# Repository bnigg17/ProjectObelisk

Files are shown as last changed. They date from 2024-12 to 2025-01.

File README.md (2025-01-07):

# Project Overview
Project Obelisk aimed to recreate and enhance the traditional key tag unlocking systems widely used for business security. Our approach replaces the physical key tag with a "custom key" powered by image recognition via artificial intelligence. The "custom key" can be any object that can be uniquely recognized, such as the back of your phone, a rubber duck, or even an apple. The system allows users to dynamically train and store custom keys, which are then used to activate a connected device, such as a servo motor. In our prototype, this servo motor simulates a door lock mechanism, showcasing the concept's functionality.

Demo

# About this Project
This project was developed over the course of 10 weeks for the Advanced Digital Systems Lab (ECE395) at UIUC. It involved the creation of a hardware-based system, where my partner and I individually or collaboratively explored the complexities of embedded systems, hardware design, and artificial intelligence. Our journey was marked by numerous challenges that required extensive research, documentation reading, and hands-on troubleshooting, pushing our knowledge and skills in electrical and embedded systems design to new limits.

# Project Obelisk
Project Obelisk is the main undertaking, designed as an all-in-one solution that integrates image processing, AI for object recognition, and a control loop to manage the servo motor and LED indicators. This system seamlessly ties together hardware and software components, allowing for dynamic key recognition and an output signal to trigger external devices.

# Project Obelisk Arduino / Raspberry Pi
The Arduino/Raspberry Pi subproject was designed as a testing environment for simpler systems and to verify our concept before moving to low-level C implementation. This step involved experimenting with synchronization signals, image array padding, and baud rate requirements for camera debugging. Using the Arduino/Raspberry Pi setup allowed us to handle some of the image processing off the primary microcontroller, providing valuable insights into data flow, timing, and system behavior.

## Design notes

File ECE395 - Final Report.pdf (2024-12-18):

# ECE 395

## Fall 2024

# Project Obelisk Final Report

Braden Nigg(bnigg2) and Ben Malone(bmalo4)

# Project Overview

Project Obelisk aimed to recreate and enhance the key tag unlocking systems commonly used for business security. Our variation eliminates the physical key tag, replacing it with a “custom key” powered by image recognition using artificial intelligence. An example of a “custom key” is really any object you could think of; the back of your phone, an apple, a rubber duck, ect. The final system allows users to train custom keys dynamically and generates an output signal to activate devices, such as a servo motor, which we used to simulate a door lock mechanism.

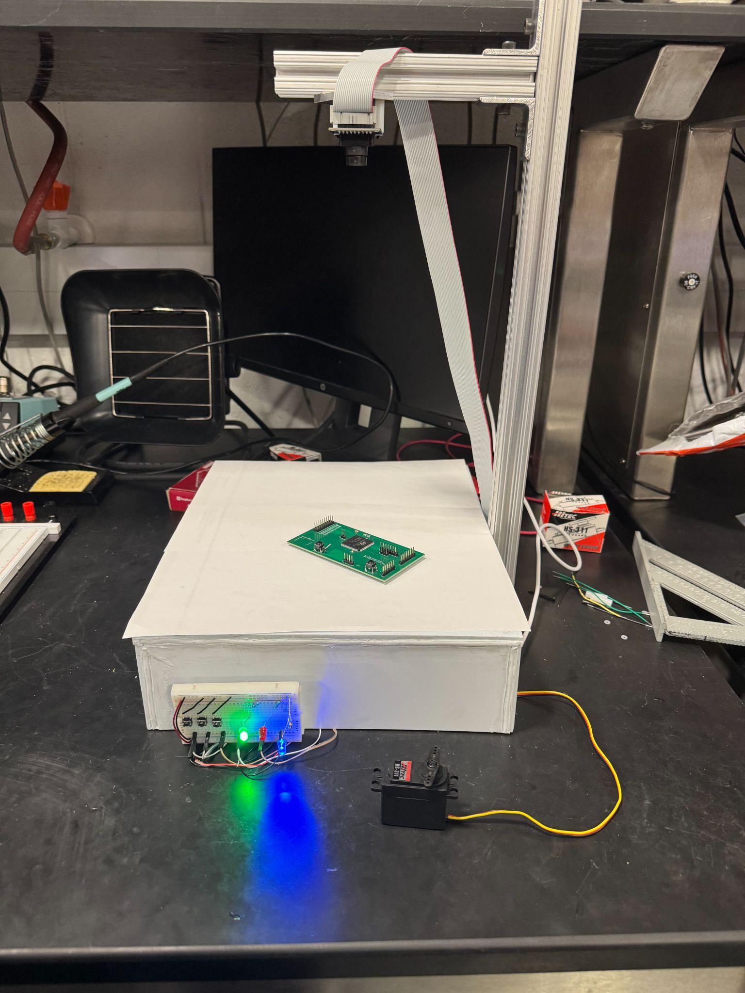
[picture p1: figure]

# Table of Contents

# System Architecture

## Components

The core component for object capture in Project Obelisk is the OV7670 camera. This camera supports a maximum resolution of 640x480 at 30 fps and offers various configurable settings for color, lighting, and scaling adjustments. It also includes an onboard algorithm for automatic image calibration, enhancing its adaptability to different environments.

Project Obelisk leverages the STM32 H7 series processor, selected for its high-frequency internal clock, which is crucial for driving the OV7670's master clock (MCLK). Additionally, its 2 MB of embedded SRAM provides sufficient capacity to run the lightweight AI algorithm utilized in the project.

The system's output component is the HS-422 servo motor. While the motor was chosen primarily for demonstration purposes in this project, those replicating the design should consider the required torque for their specific application. For our implementation, the HS-422 proved suitable for showcasing the unlocking mechanism.

## Debugging Components

We recommend using a UART device to transmit image captures to a more powerful system for analysis and validation during the calibration stages. Key considerations include the maximum baud rate supported by the UART device and the processing capability of the receiving system. For efficient transmission, we suggest a baud rate of at least 500,000 bits per second for lower resolution modes and exceeding 1 Mbit/s for full-resolution image captures. It is important to make sure the external system and the UART have matching baud rates to prevent corrupt data transmission.

## Block Diagram

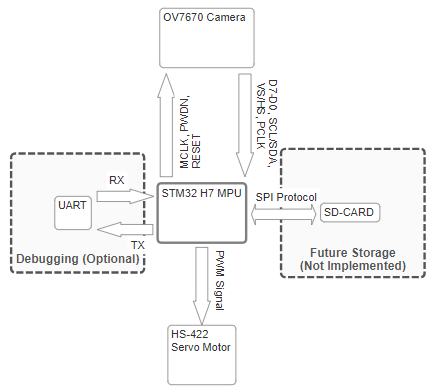
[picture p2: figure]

# Hardware Design

## Camera

The camera operates with Vcc and Vdd-IO expected at 3.0V, but it has an absolute maximum rating of 4.5V. We used 3.3V as the standard, which simplified the design by eliminating the need for additional voltage step-down circuitry.

The camera accepts a master clock input (MCLK) with a frequency range of 10–48 MHz; we chose the standard 24 MHz. However, testing revealed that the camera can operate at lower frequencies by leveraging its internal PLL (Phase Lock Loop), as described in the software section.

The pixel clock is an output signal that indicates when pixels are ready, with one pixel corresponding to two clock cycles. The camera also outputs Vsync (VS) and Hsync (HS) signals for synchronization. The Hsync signal can be modified to Href through register settings if required. In our design, these pins are not utilized as we implemented image capture based on a single snapshot. However, the Vsync signal can be valuable if the project is expanded to support a continuous live feed. Additionally, Hsync can be useful for debugging purposes, such as identifying line numbers or implementing line-based data transmissions.

Additionally, the camera provides Power Down (PWDN) and Reset pins, which can be used for power savings and setup control.

## SCCB Communication

The OV7670 camera uses the SCCB (Serial Camera Control Bus) protocol for hardware register communication. SCCB is very similar to the I2C protocol, with the key difference being that the SDA line can float in SCCB, whereas I2C requires a pull-up resistor. Despite this difference, the OV7670 can be successfully interfaced using I2C, as STM32 microcontrollers provide convenient drivers for I2C communication. By utilizing the transmit and receive functions provided by the STM32, it is possible to match the transmission sequence expected by the camera.

To ensure proper communication, pull-up resistors must be used for the SCL and SDA lines. A pull-up resistor value of 10kΩ is recommended, but it should not be lower than 4.7kΩ to maintain signal integrity. Additionally, the MCLK (Master Clock) signal must be connected to the camera; otherwise, I2C communication will not function correctly.

The OV7670 requires a 3-phase write cycle to modify its internal registers. First, a device address byte is sent, where the OV7670’s address is 0x42, with bit 0 set to 0 to indicate a write operation. If bit 0 is set to 1, it would instead indicate a read operation. Second, the subaddress byte specifies the register address to be written. Finally, a write data byte containing the desired data is transmitted to the selected register. By following this sequence, the OV7670 can reliably receive configuration data.

Reading data from the OV7670 camera follows a process similar to the write sequence but involves a 2-phase write followed by a 2-phase read. The first two bytes of the read process are identical to the 3-phase write sequence. First, the device address byte (0x42) with bit 0 set to 0 indicates a write operation, followed by the subaddress byte, which specifies the register address to be read.

After the subaddress is written, the process transitions to the read phase. Here, the device address is sent again, but this time bit 0 is set to 1, signaling a read operation. The camera then responds with the read data byte, which contains the value of the register specified in the earlier write phase. By following this sequence, the register value can be successfully read from the OV7670 camera.

SCCB Spec. Documentation

## Servo Motor

The servo motor features a simple hardware interface with a Vcc requirement of 5V, a ground connection, and a signal pin for motor control. The signal pin expects a 50 Hz PWM signal for operation. To generate this signal, we used a timer, as the required frequency is relatively slow compared to the system clock. The motor changes position based on pulse width of the PWM, and will be leveraged in the software section.

## Microcontroller

### DCMI/DMA

One of the key features of the high-performance STM32 processors is the DCMI (Digital Camera Memory Interface) driver, which simplifies the high-speed GPIO constraints when gathering image data. Enabling DCMI allows for fine control over synchronization, DMA configuration, clock signal polarity, and the specification of captured bytes and lines.

In our approach, we opted to read all bytes to capture complete pixel information and read all lines, as this allows for easier software manipulation of the image if needed. We also chose

DMA to reduce the number of read/write operations from the camera, as the pixel clock operates at speeds nearly matching that of the processor.

DMA also supports interrupts, which trigger a callback when the DMA transfer is complete, known as the frame event callback. For synchronization, we selected hardware synchronization, as the OV7670 camera generates its own hsync and vsync signals based on its internal clock and state. Finally, we specified the input as 8-bits, corresponding to D7-D0 on the OV7670, which is crucial for correctly aligning the DMA request in memory.

### Clocks

The MCU is configured to run at 168 MHz, which is more than sufficient for our use case. The primary requirement is that the AHB bus is at least 2.5 times faster than the pixel clock to ensure DMA can operate properly, as outlined in the STM32 DMA Configuration documentation. The main clock is derived from the internal high-speed clock (HSI), eliminating the need for an external oscillator. However, for greater precision, especially when working with PWM signals above 16 MHz, using an external oscillator may be preferable if available.

A Reset and Clock Control (RCC) option is used to generate a master clock out (MCO). This is necessary as timers are not clean enough at high frequencies. The MCO is configured at 24MHz and is a PLL divider down from the HSI clock.

### GPIOs and Serial Wire

Refer to the configuration document for full specifications. The I/O is primarily used to provide user control over the project’s state and to manage specific camera I/O functions. SWDIO and SWCLK are used for programming purposes and for debugging.

# Software Development

## Camera Register Setup

Below is a list of registers settings we used, there are many more and we highly recommend reading documentation. All registers are given by name and specific hex values can be found in documentation corresponding to name.

### QVGA Resolution

Register | Register Value | Description
COM3 | 0x04 | DCW - Enabled
COM14 | 0x19 | Manual scaling

SCALING_XSC | 0x3A | Scales X-Dir of Image Array
SCALING_YSC | 0x35 | Scales Y-Dir of Image Array
SCALING_DCWCTR | 0x11 | Downsampling and scaling control
SCALING_PCLK_DIV | 0xF1 | Pixel clock divider control
SCALING_PCLK_DELAY | 0x02 | Pixel clock delay control
Table 2-2 of OV7670 Implementation Guide

### RGB565 and Color Calibration

Register | Register Value | Description
COM7 | 0x04 | Camera control register, enables DCW (digital chroma width) processing.
RGB444 | 0x00 | Disable RGB444 settings
COM1 | 0x00 | Camera control register, disables CCIR656 format setting
COM15 | 0xD0 | Control for output format and compression, sets RGB output.
COM9 | 0x6A | Automatic gain control (AGC) settings, 128x Gain Ceiling
COM13 | 0x40 | Control for gamma correction, set saturation
MTX 1 | 0xB3 | Matrix coefficient 1, part of YUV to RGB conversion
MTX 2 | 0xB3 | Matrix coefficient 2, part of YUV to RGB conversion
MTX 3 | 0x00 | Matrix coefficient 3, part of YUV to RGB conversion
MTX 4 | 0x3D | Matrix coefficient 4, part of YUV to RGB conversion
MTX 5 | 0xA7 | Matrix coefficient 5, part of YUV to RGB conversion
MTX 6 | 0xE4 | Matrix coefficient 6, part of YUV to RGB conversion
Derived from Table 8-2 of OV7670 Implementation Guide Registers below the bolded line can be adjusted based on calibration needs. Registers above the bolded line are required for RGB565 to function properly.

### Frame Correction

Register | Register Value | Description
HSTART | 0x15 | Horizontal start position for the image frame. Affects where the capture begins.
HSTOP | 0x03 | Horizontal stop position for the image frame. Defines the end of the capture region in the horizontal direction.
HREF | 0x00 | Horizontal reference. Combines the start and stop positions to synchronize the horizontal scanning.
VSTART | 0x03 | Vertical start position for the image frame. Determines when the capture begins vertically.
VSTOP | 0x7B | Vertical stop position for the image frame. Defines the end of the capture region in the vertical direction.
VREF | 0x00 | Vertical reference. Combines the vertical start and stop positions to synchronize the vertical scanning.

Derived from Table 8-2 of OV7670 Implementation Guide This section may vary for each individual camera, so debugging and finding the correct values may be necessary. Essentially, it adjusts the window for capturing pixel data, where the start and stop values can behave in a modulo fashion.

### Frame Rate Control

Frame rate is crucial for continuous capture mode, but modifying the pixel clock is equally important, as synchronization signals depend on it. We chose to match the pixel clock to our master clock, which runs at 24 MHz. The camera features an internal PLL that can either be configured or bypassed. We decided to use the PLL because it produces a more stable, square pixel clock compared to the input master clock. The following equation shows how the pixel clock frequency is determined based on the input master clock.

To match obtain our 24MHz clock the following registers are manipulated:

Register | Register Value | Description
DLBV | 0x7A | Input clock x4, enable PLL
CLKRC | 0x01 | Cancels out the x4 multiplier
Derived from Table 3-2 of OV7670 Implementation Guide

## Control Flow

Our system runs continuously polling button GPIOs while in a ready state. Once a GPIO is pressed, a decoding function determines the expected next state, training one of the two images or activates the decider for if the inputted key is valid. Below is a flow graph of our system's high level control loop:

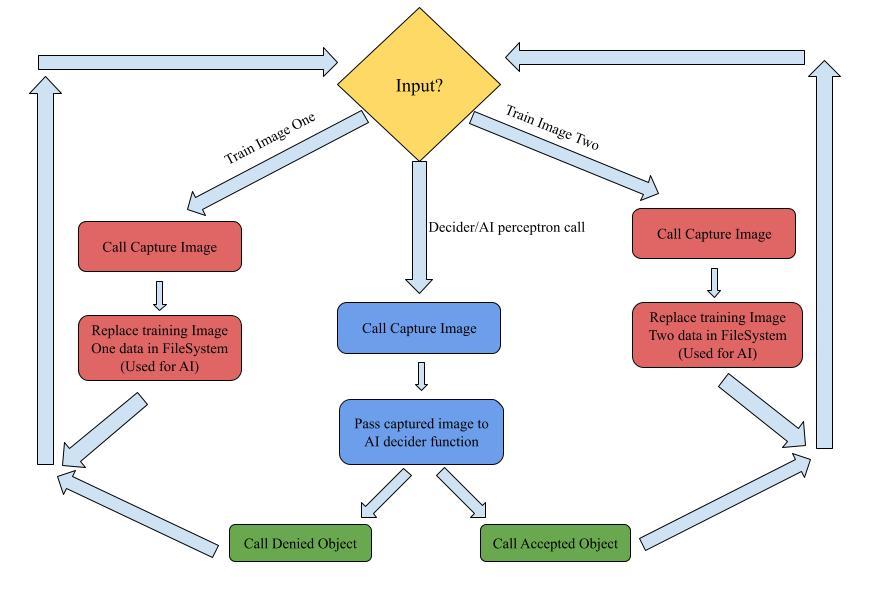
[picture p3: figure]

## Interrupts and Memory Management

Below is the memory layout for how our configured DCMI/DMA will place RGB565 values. Each word contains two pixels of complete information, as each pixel has 2 bytes of data.

Pixel X (D7 - D0) | Pixel X + 1 (D7 - D0)
RRRRRGGG | GGGBBBBB | RRRRRGGG | GGGBBBBB

With 2 MB of available embedded SRAM, we opted to create a global image buffer for the two trained images and the test image. Each image is approximately 230 KB in size when converted to RGB888, totaling 691 KB. We also have a buffer for the current capture, which is linked to our

DMA. This buffer is 153.6 KB in size, as each pixel requires two bytes from the camera. In total, 844 KB of space is required for storing the images.

The image capture works by signaling an interrupt when the DMA transfer is complete. We override the FrameEventCallback function to add our custom interrupt handler. This is where we signal that the image is ready for the intended purpose, as specified in the control loop.

## Artificial Intelligence

### Planning and System

The AI was trained on a much larger system. This allowed exploration of possibilities because of additional speed and memory, and for the ability to verify accuracy using lots of storage space for fake test images. Originally we attempted to explore the possibility of using a binary output neural network(perceptron), but because of memory constraints without off-chip memory, we had to come up with a different solution. Our solution was something like a baby-form of SURF or SIFT computer vision algorithms, which detect a variety of features about objects in images and make a decision upon them.

### Algorithm and Tuning

To be more specific, our algorithm runs an edge detection matrix multiplication on the image data in order to isolate the parts of the image which contain the object. From here a number of very defining features can be detected; object size in the specific frame, a number of different color average values, some features about the specific shape of the object. Lots of hard-tuning and auto-tuning went into finding optimized epsilon values for each of the different features, but in essence each object has a relatively personalized set of features within a reasonable epsilon which is additionally supported with a second reference image.

To ensure accuracy of the feature set method though, more data was needed to ensure that true key objects were accepted, and false images were denied(to a reasonable accuracy). So we created an image scraping tool using google images and selenium, gathered around a thousand images with a description matching the white-background environment, and tested and tuned our epsilon values again to increase accuracy. This tool and our accuracy analysis training code/tool are available in the linked github.

### AI limitations

While we put a lot of time into programming our AI code section, there are still strong limitations, as there are with all AI. Our less than 2MB ram shippable AI code is certainly no different and therefore some things won’t work. Most notably, the area in which images are taken from the camera must be where the entire object rests AND where the training images are taken. Otherwise the decider will hallucinate badly. Additionally, it is advised to avoid very non-unique objects, or objects lacking a specific color. For instance, if you trained the decider on your black wallet, there might be significant security issues considering how many black square shaped objects exist. Even worse, an all white object which could trick the edge detector, completely ruining all other feature detection mechanisms, obviously causing hallucinations.

## Servo Angle Control

As mentioned in the hardware section, the servo control input requires a 50 kHz PWM signal. To generate this signal, we need to configure the prescaler (PSC) and auto-reload register (ARR) of the timer.

For a 50 kHz PWM, we set PSC = 168-1 and ARR = 20-1. With these values, the timer produces the desired 50 kHz signal. Note these values can be of different multiples.

Next, to control the angle of the motor, we adjust the duty cycle. The following equation allows us to achieve the desired duty cycle based on the PWM period.

The key factor is that the servo motor's pulse width corresponds to the angle: a 2 ms pulse represents 180 degrees, and a 1 ms pulse represents 0 degrees. By manipulating the capture control register (CCR), we can generate the appropriate pulse width, thus controlling the motor's angle based on the desired state in the program.

# Challenges and Mitigation to Demo

## Issues

### Nucleo Prototype

The project encountered several issues during the camera calibration stages, many of which were beyond our control. Late in development we suspected that our STM32 Nucleo prototype board had a short circuit early in development. However, the board was able to program and respond to modifications for several weeks alluding us to think it was code related.

Later, we faced an issue while erasing part of the flash memory during programming. Online sources suggest this could be a command byte issue in the bootloader. However, we encountered the same problem during the PCB building stage, when the board was shorted indicating the protoboard was certainly damaged. When this error occurred on the prototype board, we could temporarily bypass it by over-volting the board, though this led to unstable behavior and program crashes.

### Custom PCB

In the PCB building phase, we successfully powered two PCBs, but after some testing, we suspected issues with both. The first PCB worked for a short time before encountering a debug authentication error during programming. This required us to drive the boot pin to boot from a different region. Further testing revealed(or maybe caused) that the board was shorted, causing the current to drop and leading to unstable program behavior. We are unsure if the debug authentication was an issue related to the hardware configuration or an advanced feature pertaining to the high end STM32 H7 chip.

The second PCB had a significant ground issue, which manifested as a triangular sine wave on the oscilloscope. Due to these challenges, we eventually ported our code and knowledge to an Arduino for demo purposes.

## Arduino Setup

### Arduino-Raspberry Pi Demo Block Diagram

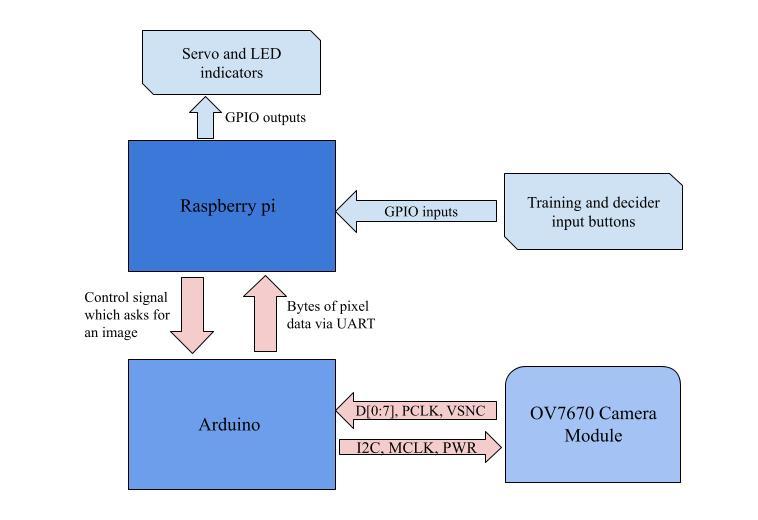
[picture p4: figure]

Our Arduino-based demo prototype required a different approach due to the limited onboard memory compared to the STM32 chip. Specifically, the Arduino lacked sufficient memory to store even a single image buffer, which made running the AI on-chip impossible. To work around this, we sent pixel data byte by byte through the UART serial line to a Raspberry Pi, which handled the memory constraints. Although we initially faced challenges with byte alignment, we were able to resolve them successfully.

Once the data reached the Raspberry Pi, it took over the processing, running a simple control loop and executing the AI code on the images received from the camera. For GPIO control, the Raspberry Pi provided a straightforward infrastructure. Instead of sending control packets back to the Arduino, we managed the limited GPIO outputs directly from the Raspberry Pi.

### Key Differences in Arduino Code

Given the limited time constraints (about 2 days) of porting our STM32 infrastructure to an arduino uno R3 we opted for merging a premade OV7670 library with our code. As much of the camera is configured through registers, there were few adjustments to be made to these settings. However, the arduino diverged from our system with not supporting DMA. The library way of gathering pixel data was to manually poll the pixel clock GPIO pin and send over UART within a time constraint. We largely left this alone as we needed a working product for the camera. The downside of this approach is very slow image capture with the combination of a slowed pixel clock and UART speeds.

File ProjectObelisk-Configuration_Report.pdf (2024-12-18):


17/12/2024

ProjectObelisk Project
Configuration Report

## 1. Description

### 1.1. Project

Project Name | ProjectObelisk
Board Name | custom
Generated with: | STM32CubeMX 6.13.0
Date | 12/17/2024

### 1.2. MCU

MCU Series | STM32H7
MCU Line | STM32H7A3/7B3
MCU name | STM32H7A3ZITxQ
MCU Package | LQFP144
MCU Pin number | 144

### 1.3. Core(s) information

Core(s) | Arm Cortex-M7

## 2. Pinout Configuration

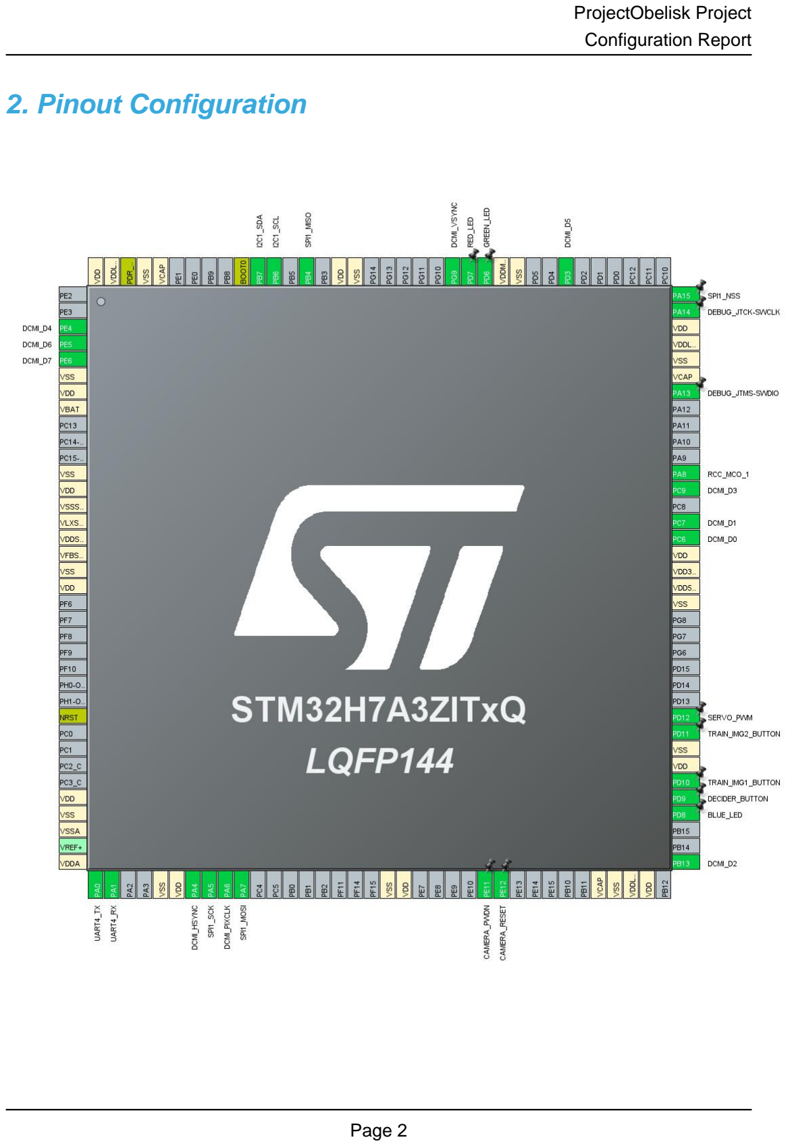
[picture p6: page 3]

## 3. Pins Configuration

Pin Number LQFP144 | Pin Name (function after reset) | Pin Type | Alternate Function(s) | Label
3 | PE4 | I/O | DCMI_D4
4 | PE5 | I/O | DCMI_D6
5 | PE6 | I/O | DCMI_D7
6 | VSS | Power
7 | VDD | Power
8 | VBAT | Power
12 | VSS | Power
13 | VDD | Power
14 | VSSSMPS | Power
15 | VLXSMPS | Power
16 | VDDSMPS | Power
17 | VFBSMPS | Power
18 | VSS | Power
19 | VDD | Power
27 | NRST | Reset
32 | VDD | Power
33 | VSS | Power
34 | VSSA | Power
36 | VDDA | Power
37 | PA0 | I/O | UART4_TX
38 | PA1 | I/O | UART4_RX
41 | VSS | Power
42 | VDD | Power
43 | PA4 | I/O | DCMI_HSYNC
44 | PA5 | I/O | SPI1_SCK
45 | PA6 | I/O | DCMI_PIXCLK
46 | PA7 | I/O | SPI1_MOSI
55 | VSS | Power
56 | VDD | Power
61 | PE11 * | I/O | GPIO_Output | CAMERA_PWDN
62 | PE12 * | I/O | GPIO_Output | CAMERA_RESET
68 | VCAP | Power
69 | VSS | Power
70 | VDDLDO | Power
71 | VDD | Power
73 | PB13 | I/O | DCMI_D2

Pin Number LQFP144 | Pin Name (function after reset) | Pin Type | Alternate Function(s) | Label
76 | PD8 * | I/O | GPIO_Output | BLUE_LED
77 | PD9 * | I/O | GPIO_Input | DECIDER_BUTTON
78 | PD10 * | I/O | GPIO_Input | TRAIN_IMG1_BUTTON
79 | VDD | Power
80 | VSS | Power
81 | PD11 * | I/O | GPIO_Input | TRAIN_IMG2_BUTTON
82 | PD12 | I/O | TIM4_CH1 | SERVO_PWM
89 | VSS | Power
90 | VDD50_USB | Power
91 | VDD33_USB | Power
92 | VDD | Power
93 | PC6 | I/O | DCMI_D0
94 | PC7 | I/O | DCMI_D1
96 | PC9 | I/O | DCMI_D3
97 | PA8 | I/O | RCC_MCO_1
102 | PA13 | I/O | DEBUG_JTMS-SWDIO
103 | VCAP | Power
104 | VSS | Power
105 | VDDLDO | Power
106 | VDD | Power
107 | PA14 | I/O | DEBUG_JTCK-SWCLK
108 | PA15 | I/O | SPI1_NSS
115 | PD3 | I/O | DCMI_D5
118 | VSS | Power
119 | VDDMMC | Power
120 | PD6 * | I/O | GPIO_Output | GREEN_LED
121 | PD7 * | I/O | GPIO_Output | RED_LED
122 | PG9 | I/O | DCMI_VSYNC
128 | VSS | Power
129 | VDD | Power
131 | PB4 | I/O | SPI1_MISO
133 | PB6 | I/O | I2C1_SCL
134 | PB7 | I/O | I2C1_SDA
135 | BOOT0 | Boot
140 | VCAP | Power
141 | VSS | Power
142 | PDR_ON | Reset
143 | VDDLDO | Power
144 | VDD | Power

* The pin is affected with an I/O function

## 4. Clock Tree Configuration

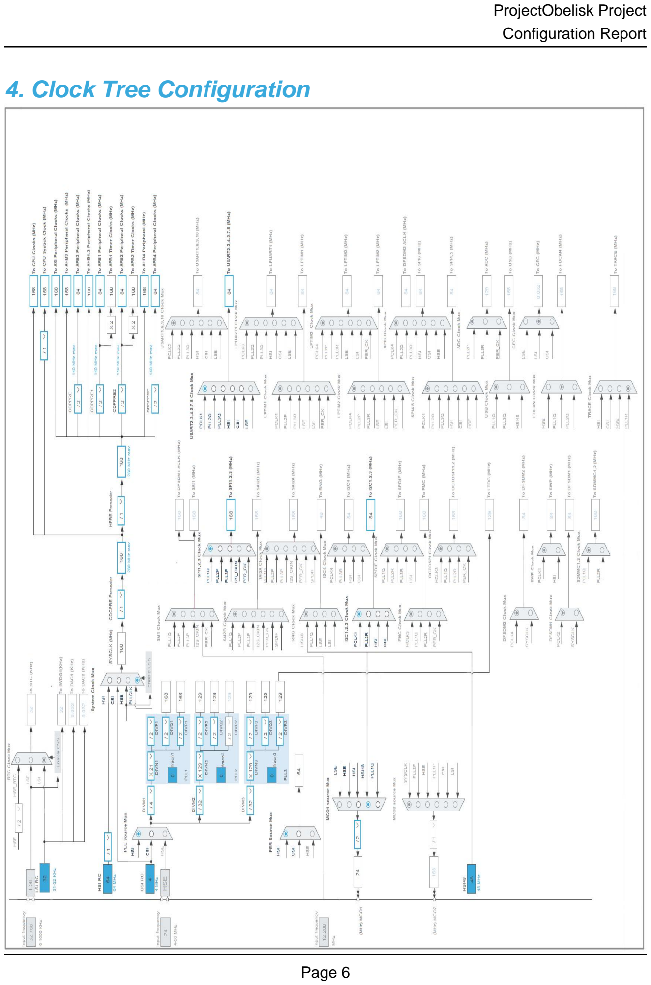
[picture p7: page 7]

## 1. Power Consumption Calculator report

### 1.1. Microcontroller Selection

Series | STM32H7
Line | STM32H7A3/7B3
MCU | STM32H7A3ZITxQ
Datasheet | DS13139_Rev0

### 1.2. Parameter Selection

Temperature | 25
Vdd | 3.0

### 1.3. Battery Selection

Battery | Li-SOCL2(A3400)
Capacity | 3400.0 mAh
Self Discharge | 0.08 %/month
Nominal Voltage | 3.6 V
Max Cont Current | 100.0 mA
Max Pulse Current | 200.0 mA
Cells in series | 1
Cells in parallel | 1

### 1.4. Sequence

Step | Step1 | Step2
Mode | RUN | STOP
Vdd | 3.0 | 3.0
Voltage Source | Battery | Battery
Range | VOS0 | SVOS5
SRDomain | DRUN | DSTOP
n/a | SRDRUN | SRDSTOP
Fetch Type | ITCM/DTCM/Cache | NA
CPU Frequency | 280 MHz | 64 MHz
Clock Configuration | HSE PLL | HSI Flash-ON
Clock Source Frequency | 16 MHz | 64 MHz
Peripherals
Additional Cons. | 0 mA | 0 mA
Average Current | 69.92 mA | 263.82 µA
Duration | 0.1 ms | 0.9 ms
DMIPS | 599.0 | 0.0
Ta Max | 115.77 | 124.97
Category | In DS Table | In DS Table

### 1.5. Results

Sequence Time | 1 ms | Average Current | 7.23 mA
Battery Life | 19 days, 14 hours Average DMIPS | | 599.2 DMIPS

### 1.6. Chart

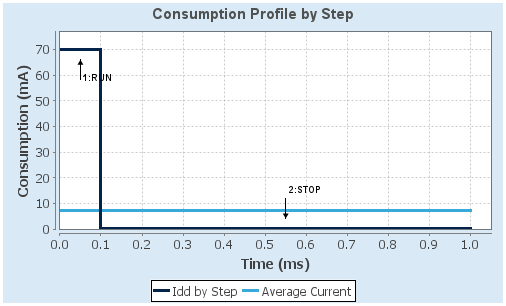
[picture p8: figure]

## 2. Software Project

### 2.1. Project Settings

Name | Value
Project Name | ProjectObelisk
Project Folder | C:\Users\BRADE\ECE395\ProjectObelisk
Toolchain / IDE | STM32CubeIDE
Firmware Package Name and Version | STM32Cube FW_H7 V1.12.0
Application Structure | Advanced
Generate Under Root | Yes
Do not generate the main() | No
Minimum Heap Size | 0x200
Minimum Stack Size | 0x400

### 2.2. Code Generation Settings

Name | Value
STM32Cube MCU packages and embedded software | Copy only the necessary library files
Generate peripheral initialization as a pair of '.c/.h' files | No
Backup previously generated files when re-generating | No
Keep User Code when re-generating | Yes
Delete previously generated files when not re-generated | Yes
Set all free pins as analog (to optimize the power consumption) | No
Enable Full Assert | No

### 2.3. Advanced Settings - Generated Function Calls

Rank | Function Name | Peripheral Instance Name
1 | SystemClock_Config | RCC
2 | MX_GPIO_Init | GPIO
3 | MX_DMA_Init | DMA
4 | MX_DCMI_Init | DCMI
5 | MX_I2C1_Init | I2C1
6 | MX_SPI1_Init | SPI1
7 | MX_UART4_Init | UART4
8 | MX_TIM4_Init | TIM4

## 3. Peripherals and Middlewares Configuration

### 3.1. CORTEX_M7

3.1.1. Parameter Settings:

Speculation default mode Settings:

Speculation default mode | Enabled *
Cortex Interface Settings:
CPU ICache | Disabled
CPU DCache | Disabled
Cortex Memory Protection Unit Control Settings:
MPU Control Mode | Background Region Privileged accesses only + MPU Disabled during hard fault, NMI and FAULTMASK handlers

Cortex Memory Protection Unit Region 0 Settings:

MPU Region | Enabled
MPU Region Base Address | 0x0 *
MPU Region Size | 4GB
MPU SubRegion Disable | 0x87 *
MPU TEX field level | level 0
MPU Access Permission | ALL ACCESS NOT PERMITTED
MPU Instruction Access | DISABLE
MPU Shareability Permission | ENABLE
MPU Cacheable Permission | DISABLE
MPU Bufferable Permission | DISABLE
Cortex Memory Protection Unit Region 1 Settings:
MPU Region | Disabled
Cortex Memory Protection Unit Region 2 Settings:
MPU Region | Disabled
Cortex Memory Protection Unit Region 3 Settings:
MPU Region | Disabled
Cortex Memory Protection Unit Region 4 Settings:
MPU Region | Disabled
Cortex Memory Protection Unit Region 5 Settings:
MPU Region | Disabled
Cortex Memory Protection Unit Region 6 Settings:
MPU Region | Disabled
Cortex Memory Protection Unit Region 7 Settings:
MPU Region | Disabled
Cortex Memory Protection Unit Region 8 Settings:
MPU Region | Disabled

Cortex Memory Protection Unit Region 9 Settings:

MPU Region | Disabled
Cortex Memory Protection Unit Region 10 Settings:
MPU Region | Disabled
Cortex Memory Protection Unit Region 11 Settings:
MPU Region | Disabled
Cortex Memory Protection Unit Region 12 Settings:
MPU Region | Disabled
Cortex Memory Protection Unit Region 13 Settings:
MPU Region | Disabled
Cortex Memory Protection Unit Region 14 Settings:
MPU Region | Disabled
Cortex Memory Protection Unit Region 15 Settings:
MPU Region | Disabled

### 3.2. DCMI

DCMI: Slave 8 bits External Synchro
3.2.1. Parameter Settings:

Mode Config:
Pixel clock polarity | Active on Rising edge *
Vertical synchronization polarity | Active High *
Horizontal synchronization polarity | Active Low
Frequency of frame capture | All frames are captured
JPEG mode | Disabled
Interface Capture Config:
Byte Select Mode | Interface captures all received bytes
Line Select Mode | Interface captures all received lines

### 3.3. DEBUG

Debug: Serial Wire

### 3.4. I2C1

I2C: I2C
3.4.1. Parameter Settings:

Timing configuration:

Custom Timing | Disabled
I2C Speed Mode | Standard Mode
I2C Speed Frequency (KHz) | 100
Rise Time (ns) | 0
Fall Time (ns) | 0
Coefficient of Digital Filter | 0
Analog Filter | Enabled
Timing | 0x10A0A4F8 *
Slave Features:
Clock No Stretch Mode | Disabled
General Call Address Detection | Disabled
Primary Address Length selection | 7-bit
Dual Address Acknowledged | Disabled
Primary slave address | 0

### 3.5. MEMORYMAP

mode: Activated

### 3.6. RCC

mode: Master Clock Output 1
3.6.1. Parameter Settings:

Power Parameters:

SupplySource | PWR_DIRECT_SMPS_SUPPLY
Power Regulator Voltage Scale | Power Regulator Voltage Scale 1
RCC Parameters:
TIM Prescaler Selection | Disabled
HSE Startup Timout Value (ms) | 100
LSE Startup Timout Value (ms) | 5000
CSI Calibration Value | 16
HSI Calibration Value | 64
System Parameters:
VDD voltage (V) | 3.3
Flash Latency(WS) | 4 WS (5 CPU cycle)
PLL range Parameters:
PLL1 input frequency range | Between 8 and 16 MHz
PLL1 clock Output range | Wide VCO range

### 3.7. SPI1

Mode: Full-Duplex Master
Hardware NSS Signal: Hardware NSS Input Signal
3.7.1. Parameter Settings:

Basic Parameters:

Frame Format | Motorola
Data Size | 4 Bits
First Bit | MSB First
Clock Parameters:
Prescaler (for Baud Rate) | 2
Baud Rate | 84.0 MBits/s *
Clock Polarity (CPOL) | Low
Clock Phase (CPHA) | 1 Edge
Advanced Parameters:
CRC Calculation | Disabled
NSSP Mode | Enabled
NSS Signal Type | Input Hardware
Fifo Threshold | Fifo Threshold 01 Data
Tx Crc Initialization Pattern | All Zero Pattern
Rx Crc Initialization Pattern | All Zero Pattern
Nss Polarity | Nss Polarity Low
Master Ss Idleness | 00 Cycle
Master Inter Data Idleness | 00 Cycle
Master Receiver Auto Susp | Disable
Master Keep Io State | Master Keep Io State Disable
IO Swap | Disabled

### 3.8. SYS

Timebase Source: SysTick

### 3.9. TIM4

Clock Source : Internal Clock Channel1: PWM Generation CH1
3.9.1. Parameter Settings:

Counter Settings:

Prescaler (PSC - 16 bits value) | 168-1 *
Counter Mode | Up
Counter Period (AutoReload Register - 16 bits value ) | 20-1 *
Internal Clock Division (CKD) | No Division
auto-reload preload | Disable
Trigger Output (TRGO) Parameters:
Master/Slave Mode (MSM bit) | Disable (Trigger input effect not delayed)
Trigger Event Selection TRGO | Reset (UG bit from TIMx_EGR)
Clear Input:
Clear Input Source | Disable
PWM Generation Channel 1:
Mode | PWM mode 1
Pulse (16 bits value) | 0
Output compare preload | Enable
Fast Mode | Disable
CH Polarity | High

### 3.10. UART4

Mode: Asynchronous
3.10.1. Parameter Settings:

Basic Parameters:

Baud Rate | 19200 *
Word Length | 8 Bits (including Parity)
Parity | None
Stop Bits | 1
Advanced Parameters:
Data Direction | Receive and Transmit
Over Sampling | 16 Samples
Single Sample | Disable
ClockPrescaler | 1
Fifo Mode | FIFO mode disable
Txfifo Threshold | 1 eighth full configuration
Rxfifo Threshold | 1 eighth full configuration
Advanced Features:
Auto Baudrate | Disable
TX Pin Active Level Inversion | Disable

RX Pin Active Level Inversion | Disable
Data Inversion | Disable
TX and RX Pins Swapping | Disable
Overrun | Enable
DMA on RX Error | Enable
MSB First | Disable

* User modified value

## 4. System Configuration

### 4.1. GPIO configuration

IP | Pin | Signal | GPIO mode | GPIO pull/up pull down | Max Speed | User Label
| | | | | *
| PE5 | DCMI_D6 | Alternate Function Push Pull | Pull-down * | Very High *
| PE6 | DCMI_D7 | Alternate Function Push Pull | Pull-down * | Very High *
| PA4 | DCMI_HSYNC | Alternate Function Push Pull | Pull-down * | Very High *
| PA6 | DCMI_PIXCLK | Alternate Function Push Pull | Pull-down * | Very High *
| PB13 | DCMI_D2 | Alternate Function Push Pull | Pull-down * | Very High *
| PC6 | DCMI_D0 | Alternate Function Push Pull | Pull-down * | Very High *
| PC7 | DCMI_D1 | Alternate Function Push Pull | Pull-down * | Very High *
| PC9 | DCMI_D3 | Alternate Function Push Pull | Pull-down * | Very High *
| PD3 | DCMI_D5 | Alternate Function Push Pull | Pull-down * | Very High *
| PG9 | DCMI_VSYNC | Alternate Function Push Pull | Pull-down * | Very High *
DEBUG | PA13 | DEBUG_JTMS-SWDIO | n/a | n/a | n/a
| PA14 | DEBUG_JTCK-SWCLK | n/a | n/a | n/a
I2C1 | PB6 | I2C1_SCL | Alternate Function Open Drain | No pull-up and no pull-down | Low
| PB7 | I2C1_SDA | Alternate Function Open Drain | No pull-up and no pull-down | Low
RCC | PA8 | RCC_MCO_1 | Alternate Function Push Pull | No pull-up and no pull-down | Very High *
SPI1 | PA5 | SPI1_SCK | Alternate Function Push Pull | No pull-up and no pull-down | Low
| PA7 | SPI1_MOSI | Alternate Function Push Pull | No pull-up and no pull-down | Low
| PA15 | SPI1_NSS | Alternate Function Push Pull | No pull-up and no pull-down | Low
DCMI | PE4 | DCMI_D4 | Alternate Function Push Pull | Pull-down * | Very High

IP | Pin | Signal | GPIO mode | GPIO pull/up pull down | Max Speed | User Label
| PB4 | SPI1_MISO | Alternate Function Push Pull | No pull-up and no pull-down | Low
TIM4 | PD12 | TIM4_CH1 | Alternate Function Push Pull | No pull-up and no pull-down | Low | SERVO_PWM
UART4 | PA0 | UART4_TX | Alternate Function Push Pull | No pull-up and no pull-down | Low
| PA1 | UART4_RX | Alternate Function Push Pull | No pull-up and no pull-down | Low
GPIO | PE11 | GPIO_Output | Output Push Pull | No pull-up and no pull-down | Low | CAMERA_PWDN
| PE12 | GPIO_Output | Output Push Pull | No pull-up and no pull-down | Low | CAMERA_RESET
| PD8 | GPIO_Output | Output Push Pull | No pull-up and no pull-down | Low | BLUE_LED
| PD9 | GPIO_Input | Input mode | No pull-up and no pull-down | n/a | DECIDER_BUTTON
| PD10 | GPIO_Input | Input mode | No pull-up and no pull-down | n/a | TRAIN_IMG1_BUTTON
| PD11 | GPIO_Input | Input mode | No pull-up and no pull-down | n/a | TRAIN_IMG2_BUTTON
| PD6 | GPIO_Output | Output Push Pull | No pull-up and no pull-down | Low | GREEN_LED
| PD7 | GPIO_Output | Output Push Pull | No pull-up and no pull-down | Low | RED_LED

### 4.2. DMA configuration

DMA request | Stream | Direction | Priority
DCMI | DMA1_Stream0 | Peripheral To Memory | Low

DCMI: DMA1_Stream0 DMA request Settings:

Mode: | Normal
Use fifo: | Disable
Peripheral Increment: | Disable
Memory Increment: | Enable *
Peripheral Data Width: | Word *
Memory Data Width: | Word

### 4.3. BDMA1 configuration

nothing configured in DMA service

### 4.4. BDMA2 configuration

nothing configured in DMA service

### 4.5. MDMA configuration

nothing configured in DMA service

### 4.6. NVIC configuration

4.6.1. NVIC
Interrupt Table | Enable | Preenmption Priority | SubPriority
Non maskable interrupt | true | 0 | 0
Hard fault interrupt | true | 0 | 0
Memory management fault | true | 0 | 0
Pre-fetch fault, memory access fault | true | 0 | 0
Undefined instruction or illegal state | true | 0 | 0
System service call via SWI instruction | true | 0 | 0
Debug monitor | true | 0 | 0
Pendable request for system service | true | 0 | 0
System tick timer | true | 15 | 0
DMA1 stream0 global interrupt | true | 0 | 0
DCMI and PSSI global interrupt | true | 0 | 0
PVD and PVM interrupts through EXTI line | unused
Flash global interrupt | unused
RCC global interrupt | unused
TIM4 global interrupt | unused
I2C1 event interrupt | unused
I2C1 error interrupt | unused
SPI1 global interrupt | unused
UART4 global interrupt | unused
FPU global interrupt | unused
HSEM1 global interrupt | unused
4.6.2. NVIC Code generation
Enabled interrupt Table | Select for init sequence ordering | Generate IRQ handler | Call HAL handler
Non maskable interrupt | false | true | false
Hard fault interrupt | false | true | false
Memory management fault | false | true | false
Pre-fetch fault, memory access fault | false | true | false
Undefined instruction or illegal state | false | true | false
System service call via SWI instruction | false | true | false
Debug monitor | false | true | false
Pendable request for system service | false | true | false
System tick timer | false | true | true
DMA1 stream0 global interrupt | false | true | true
DCMI and PSSI global interrupt | false | true | true

* User modified value

## 5. System Views

5.1. Category view
5.1.1. Current

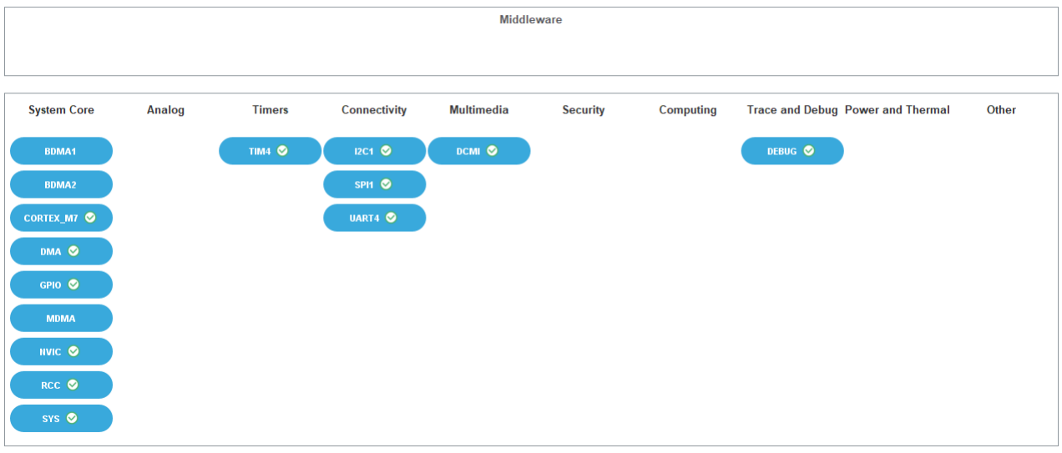
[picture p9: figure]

## 6. Docs & Resources

Type | Link
BSDL files | https://www.st.com/resource/en/bsdl_model/stm32h7_bsdl.zip
IBIS models | https://www.st.com/resource/en/ibis_model/stm32h7_ibis.zip
System View Description | https://www.st.com/resource/en/svd/stm32h7-svd.zip
Presentations | https://www.st.com/resource/en/product_presentation/microcontrollers_stm32h7_series_product_overview.pdf
Presentations | https://www.st.com/resource/en/product_presentation/stm32-stm8_embedded_software_solutions.pdf
Presentations | https://www.st.com/resource/en/product_presentation/stm32_eval-tools_portfolio.pdf
Presentations | https://www.st.com/resource/en/product_presentation/stm32_stm8_functi onal-safety-packages.pdf
Presentations | https://www.st.com/resource/en/product_presentation/stm32-stm8_software_development_tools.pdf
Presentations | https://www.st.com/resource/en/product_presentation/microcontrollers_stm32h7a3-b3_line_product-overview.pdf
Presentations | https://www.st.com/resource/en/product_presentation/microcontrollers-stm32-family-overview.pdf
Presentations | https://www.st.com/resource/en/product_presentation/microcontrollers-stm32h7rs-lines-overview.pdf
Brochures | https://www.st.com/resource/en/brochure/brstm32h7.pdf
Brochures | https://www.st.com/resource/en/brochure/products-and-solutions-for-plcs-and-smart-i-os.pdf
Flyers | https://www.st.com/resource/en/flyer/flstm32nucleo.pdf
Flyers | https://www.st.com/resource/en/flyer/flstm32trust.pdf
Flyers | https://www.st.com/resource/en/flyer/flstm32h7rs.pdf
Application Notes | https://www.st.com/resource/en/application_note/an1709-emc-design-guide-for-stm8-stm32-and-legacy-mcus-stmicroelectronics.pdf
Application Notes | https://www.st.com/resource/en/application_note/an2606-stm32-

| microcontroller-system-memory-boot-mode-stmicroelectronics.pdf
Application Notes | https://www.st.com/resource/en/application_note/an2639-soldering-recommendations-and-package-information-for-leadfree-ecopack-mcus-and-mpus-stmicroelectronics.pdf
Application Notes | https://www.st.com/resource/en/application_note/an3126-audio-and-waveform-generation-using-the-dac-in-stm32-products-stmicroelectronics.pdf
Application Notes | https://www.st.com/resource/en/application_note/an3155-usart-protocol-used-in-the-stm32-bootloader-stmicroelectronics.pdf
Application Notes | https://www.st.com/resource/en/application_note/an3156-usb-dfu-protocol-used-in-the-stm32-bootloader-stmicroelectronics.pdf
Application Notes | https://www.st.com/resource/en/application_note/an4221-i2c-protocol-used-in-the-stm32-bootloader-stmicroelectronics.pdf
Application Notes | https://www.st.com/resource/en/application_note/an4286-spi-protocol-used-in-the-stm32-bootloader-stmicroelectronics.pdf
Application Notes | https://www.st.com/resource/en/application_note/an4566-extending-the-dac-performance-of-stm32-microcontrollers-stmicroelectronics.pdf
Application Notes | https://www.st.com/resource/en/application_note/an4655-virtually-increasing-the-number-of-serial-communication-peripherals-in-stm32-applications-stmicroelectronics.p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
Application Notes | https://www.st.com/resource/en/application_note/an4750-handling-of-soft-errors-in-stm32-applications-stmicroelectronics.pdf
Application Notes | https://www.st.com/resource/en/application_note/an4776-generalpurpose-timer-cookbook-for-stm32-microcontrollers-stmicroelectronics.pdf
Application Notes | https://www.st.com/resource/en/application_note/an4803-highspeed-si-simulations-using-ibis-and-boardlevel-simulations-using-hyperlynx-si-on-stm32-mcus-and-mpus-stmic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
Application Notes | https://www.st.com/resource/en/application_note/an4839-level-1-cache-on-stm32f7-series-and-stm32h7-series-stmicroelectronics.pdf
Application Notes | https://www.st.com/resource/en/application_note/an4989-stm32-microcontroller-debug-toolbox-stmicroelectronics.pdf
Application Notes | https://www.st.com/resource/en/application_note/an4990-getting-started- with-sigmadelta-digital-interface-on-applicable-stm32-microcontrollers-

| stmicroelectronics.pdf
Application Notes | https://www.st.com/resource/en/application_note/an5020-digital-camera-interface-dcmi-on-stm32-mcus-stmicroelectronics.pdf
Application Notes | https://www.st.com/resource/en/application_note/an5027-interfacing-pdm-digital-microphones-using-stm32-mcus-and-mpus-stmicroelectronics.pdf
Application Notes | https://www.st.com/resource/en/application_note/an5033-stm32cube-mcu-package-examples-for-stm32h7-series-stmicroelectronics.pdf
Application Notes | https://www.st.com/resource/en/application_note/an5073-receiving-spdif-audio-stream-with-the-stm32f4f7h7-series-stmicroelectronics.pdf
Application Notes | https://www.st.com/resource/en/application_note/an5307-getting-started-with-stm32h7a37b3-line-and-stm32h7b0-value-line-microcontroller-hardware-development-stmicroel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
Application Notes | https://www.st.com/resource/en/application_note/an4899-stm32-microcontroller-gpio-hardware-settings-and-lowpower-consumption-stmicroelectronics.pdf
Application Notes | https://www.st.com/resource/en/application_note/an5450-stm32h7a37b3-lines-and-stm32h7b0-value-line-smart-power-management-expansion-package-for-stm32cube-stmicroelec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
Application Notes | https://www.st.com/resource/en/application_note/an5612-esd-protection-of-stm32-mcus-and-mpus-stmicroelectronics.pdf
Application Notes | https://www.st.com/resource/en/application_note/an5293-migration-guide-from-stm32f7-series-to-stmh74x75x-stm32h72x73x-and-stmh7a37bx-devices-stmicroelectronics.pdf
Application Notes | https://www.st.com/resource/en/application_note/an4838-introduction-to-memory-protection-unit-management-on-stm32-mcus-stmicroelectronics.pdf
Application Notes | https://www.st.com/resource/en/application_note/an5927-i3c-protocol-used-in-the-stm32-bootloader-stmicroelectronics.pdf
Application Notes | https://www.st.com/resource/en/application_note/an5225-introduction-to-usb-typec-power-delivery-for-stm32-mcus-and-mpus-stmicroelectronics.pdf
Application Notes | https://www.st.com/resource/en/application_note/an5342--how-to-use- error-correction-code-ecc-management-for-internal-memories-protection-

| on-stm32-mcus-stmicroelectronics.pdf
Application Notes | https://www.st.com/resource/en/application_note/an2834-how-to-optimize-the-adc-accuracy-in-the-stm32-mcus-stmicroelectronics.pdf
Application Notes | https://www.st.com/resource/en/application_note/an5537-how-to-use-adc-oversampling-techniques-to-improve-signaltonoise-ratio-on-stm32-mcus-stmicroelectronics.pdf
Application Notes | https://www.st.com/resource/en/application_note/an5036-guidelines-for-thermal-management-on-stm32-applications-stmicroelectronics.pdf
Application Notes | https://www.st.com/resource/en/application_note/an5405-how-to-use-fdcan-bootloader-protocol-on-stm32-mcus-stmicroelectronics.pdf
Application Notes | https://www.st.com/resource/en/application_note/an5690-how-to-use-vrefbuf-peripheral-on-stm32-mcus-and-mpus-stmicroelectronics.pdf
Application Notes | https://www.st.com/resource/en/application_note/an4230-introduction-to-random-number-generation-validation-using-the-nist-statistical-test-suite-for-stm32-mcus-and-m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
Application Notes | https://www.st.com/resource/en/application_note/an2867-guidelines-for-oscillator-design-on-stm8afals-and-stm32-mcusmpus-stmicroelectronics.pdf
Application Notes | https://www.st.com/resource/en/application_note/an4013-introduction-to-timers-for-stm32-mcus-stmicroelectronics.pdf
Application Notes | https://www.st.com/resource/en/application_note/an4277-how-to-use-pwm-shutdown-for-motor-control-and-digital-power-conversion-on-stm32-mcus-stmicroelectronics.pdf
Application Notes | https://www.st.com/resource/en/application_note/an4635-how-to-optimize-lpuart-power-consumption-on-stm32-mcus-stmicroelectronics.pdf
Application Notes | https://www.st.com/resource/en/application_note/an4759-introduction-to-using-the-hardware-realtime-clock-rtc-and-the-tamper-management-unit-tamp-with-stm32-mcus-stmi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
Application Notes | https://www.st.com/resource/en/application_note/an4861-introduction-to-lcdtft-display-controller-ltdc-on-stm32-mcus-stmicroelectronics.pdf
Application Notes | https://www.st.com/resource/en/application_note/an4908-getting-started- with-usart-automatic-baud-rater-detection-for-stm32-mcus-

| stmicroelectronics.pdf
Application Notes | https://www.st.com/resource/en/application_note/an4943-how-to-use-chromart-accelerator-to-refresh-an-lcdtft-display-on-stm32-mcus-stmicroelectronics.pdf
Application Notes | https://www.st.com/resource/en/application_note/an5156-introduction-to-security-for-stm32-mcus-stmicroelectronics.pdf
Application Notes | https://www.st.com/resource/en/application_note/an5200-getting-started-with-stm32h7-mcus-sdmmc-host-controller-stmicroelectronics.pdf
Application Notes | https://www.st.com/resource/en/application_note/an5224-introduction-to-dmamux-for-stm32-mcus-stmicroelectronics.pdf
Application Notes | https://www.st.com/resource/en/application_note/an5507-how-to-use-crc-to-check-the-integrity-of-the-internal-flash-memory-on-stm32h7-mcus-stmicroelectronics.pdf
Application Notes | https://www.st.com/resource/en/application_note/an5543-guidelines-for-enhanced-spi-communication-on-stm32-mcus-and-mpus-stmicroelectronics.pdf
Application Notes | https://www.st.com/resource/en/application_note/an5050-getting-started-with-octospi-hexadecaspi-and-xspi-interface-on-stm32-mcus-stmicroelectronics.pdf
Application Notes | https://www.st.com/resource/en/application_note/an4996-how-to-use-the-jpeg-codec-peripheral-on-stm32-mcus-stmicroelectronics.pdf
Application Notes | https://www.st.com/resource/en/application_note/an5348-introduction-to-fdcan-peripherals-for-stm32-mcus-stmicroelectronics.pdf
Application Notes for related Tools & Software | https://www.st.com/resource/en/application_note/an1202_freertos_guide-freertos-guide-stmicroelectronics.pdf
Application Notes for related Tools & Software | https://www.st.com/resource/en/application_note/an1602_semihosting_in_truestudio-how-to-do-semihosting-in-truestudio-stmicroelectronics.pdf
Application Notes for related Tools & Software | https://www.st.com/resource/en/application_note/an1801_stm32cubeprogrammer_in_truestudio-installing-stm32cubeprogrammer-in-truestudio-stmicroelectronics.pdf
Application Notes | https://www.st.com/resource/en/application_note/atollic_editing_keyboard

for related Tools & Software | _shortcuts-atollic-editing-keyboard-shortcuts-stmicroelectronics.pdf
Application Notes for related Tools & Software | https://www.st.com/resource/en/application_note/iar_to_atollic_truestudio_migration_guide-truestudio-for-arm-migration-guide-iar-embedded-workbench-to-truestudio-stm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
Application Notes for related Tools & Software | https://www.st.com/resource/en/application_note/stm32cubemx_installation_in_truestudio-stm32cubemx-installation-in-truestudio-stmicroelectronics.pdf
Application Notes for related Tools & Software | https://www.st.com/resource/en/application_note/an2606-stm32-microcontroller-system-memory-boot-mode-stmicroelectronics.pdf
Application Notes for related Tools & Software | https://www.st.com/resource/en/application_note/an4323-getting-started-with-stemwin-library-stmicroelectronics.pdf
Application Notes for related Tools & Software | https://www.st.com/resource/en/application_note/an4435-guidelines-for-obtaining-ulcsaiec-607301603351-class-b-certification-in-any-stm32-application-stmicroelectroni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
Application Notes for related Tools & Software | https://www.st.com/resource/en/application_note/an4657-stm32-inapplication-programming-iap-using-the-usart-stmicroelectronics.pdf
Application Notes for related Tools & Software | https://www.st.com/resource/en/application_note/an4841-digital-signal-processing-for-stm32-microcontrollers-using-cmsis-stmicroelectronics.pdf
Application Notes for related Tools & Software | https://www.st.com/resource/en/application_note/an4891-stm32h72x-stm32h73x-and-singlecore-stm32h74x75x-system-architecture-and-performance-stmicroelectronics.pdf
Application Notes for related Tools & Software | https://www.st.com/resource/en/application_note/an5001-stm32cube-expansion-package-for-stm32h7-series-mdma-stmicroelectronics.pdf
Application Notes for related Tools & Software | https://www.st.com/resource/en/application_note/an5014-stm32h7x3-smart-power-management-expansion-package-for-stm32cube-stmicroelectronics.pdf

Application Notes
for related Tools

https://www.st.com/resource/en/application_note/an5033-stm32cubemcu-package-examples-for-stm32h7-series-stmicroelectronics.pdf

& Software
Application Notes for related Tools & Software | https://www.st.com/resource/en/application_note/an5056-integration-guide-for-the-xcubesbsfu-stm32cube-expansion-package-stmicroelectronics.pdf
Application Notes for related Tools & Software | https://www.st.com/resource/en/application_note/an5360-getting-started-with-projects-based-on-the-stm32mp1-series-in-stm32cubeide-stmicroelectronics.pdf
Application Notes for related Tools & Software | https://www.st.com/resource/en/application_note/an5361-getting-started-with-projects-based-on-dualcore-stm32h7-microcontrollers-in-stm32cubeide-stmicroelectronics.pd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
Application Notes for related Tools & Software | https://www.st.com/resource/en/application_note/an5394-getting-started-with-projects-based-on-the-stm32l5-series-in-stm32cubeide-stmicroelectronics.pdf
Application Notes for related Tools & Software | https://www.st.com/resource/en/application_note/an5418-how-to-build-a-simple-usbpd-sink-application-with-stm32cubemx-stmicroelectronics.pdf
Application Notes for related Tools & Software | https://www.st.com/resource/en/application_note/an5426-migrating-graphics-middleware-projects-from-stm32cubemx-540-to-stm32cubemx-550-stmicroelectronics.pdf
Application Notes for related Tools & Software | https://www.st.com/resource/en/application_note/an5564-getting-started-with-projects-based-on-dualcore-stm32wl-microcontrollers-in-stm32cubeide-stmicroelectronics.pd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
Application Notes for related Tools & Software | https://www.st.com/resource/en/application_note/an4865-lowpower-timer-lptim-applicative-use-cases-on-stm32-mcus-and-mpus-stmicroelectronics.pdf
Application Notes for related Tools & Software | https://www.st.com/resource/en/application_note/an5698-adapting-the-xcubestl-functional-safety-package-for-stm32-iec-61508-compliant-to-other-safety-standards-stmicr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
Application Notes for related Tools & Software | https://www.st.com/resource/en/application_note/an5731-stm32cubemx-and-stm32cubeide-threadsafe-solution-stmicroelectronics.pdf
Application Notes for related Tools & Software | https://www.st.com/resource/en/application_note/an5450-stm32h7a37b3-lines-and-stm32h7b0-value-line-smart-power-management-expansion-package-for-stm32cube-stmicroelec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

Application Notes for related Tools & Software | https://www.st.com/resource/en/application_note/an4502-stm32-smbuspmbus-expansion-package-for-stm32cube-stmicroelectronics.pdf
Application Notes for related Tools & Software | https://www.st.com/resource/en/application_note/an5952-how-to-use-cmake-in-stm32cubeide-stmicroelectronics.pdf
Application Notes for related Tools & Software | https://www.st.com/resource/en/application_note/an4635-how-to-optimize-lpuart-power-consumption-on-stm32-mcus-stmicroelectronics.pdf
Application Notes for related Tools & Software | https://www.st.com/resource/en/application_note/an5054-how-to-perform-secure-programming-using-stm32cubeprogrammer-stmicroelectronics.pdf
Application Notes for related Tools & Software | https://www.st.com/resource/en/application_note/an6088-how-to-use-mce-for-encryptiondecryption-on-stm32-mcus-stmicroelectronics.pdf
Design Notes & Tips | https://www.st.com/resource/en/design_tip/dt0117-microphone-array-beamforming-in-the-pcm-and-pdm-domain-stmicroelectronics.pdf
Errata Sheets | https://www.st.com/resource/en/errata_sheet/es0478-stm32h7a3xig-stm32h7b0xb-and-stm32h7b3xi-device-errata-stmicroelectronics.pdf
Datasheet | https://www.st.com/resource/en/datasheet/dm00674683.pdf
Programming Manuals | https://www.st.com/resource/en/programming_manual/pm0253-stm32f7-series-and-stm32h7-series-cortexm7-processor-programming-manual-stmicroelectronics.pdf
Reference Manuals | https://www.st.com/resource/en/reference_manual/rm0455-stm32h7a37b3-and-stm32h7b0-value-line-advanced-armbased-32bit-mcus-stmicroelectronics.pdf
Technical Notes & Articles | https://www.st.com/resource/en/technical_note/tn1163-description-of-wlcsp-for-microcontrollers-and-recommendations-for-its-use-stmicroelectronics.pdf
Technical Notes & Articles | https://www.st.com/resource/en/technical_note/tn1204-tape-and-reel-shipping-media-for-stm32-microcontrollers-in-bga-packages-stmicroelectronics.pdf

Technical Notes
& Articles

https://www.st.com/resource/en/technical_note/tn1205-tape-and-reelshipping-media-for-stm8-and-stm32-microcontrollers-in-fpn-packages-

| stmicroelectronics.pdf
Technical Notes & Articles | https://www.st.com/resource/en/technical_note/tn1206-tape-and-reel-shipping-media-for-stm8-and-stm32-microcontrollers-in-qfp-packages-stmicroelectronics.pdf
Technical Notes & Articles | https://www.st.com/resource/en/technical_note/tn1207-tape-and-reel-shipping-media-for-stm8-and-stm32-microcontrollers-in-so-packages-stmicroelectronics.pdf
Technical Notes & Articles | https://www.st.com/resource/en/technical_note/tn1208-tape-and-reel-shipping-media-for-stm8-and-stm32-microcontrollers-in-tssop-and-ssop-packages-stmicroelectronics.p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
Technical Notes & Articles | https://www.st.com/resource/en/technical_note/tn1433-reference-device-marking-schematics-for-stm32-microcontrollers-and-microprocessors-stmicroelectronics.pdf
Technical Notes & Articles | https://www.st.com/resource/en/technical_note/tn1489-security-bulletin-tn1489stpsirt-physical-attacks-on-stm32-and-stm32cube-firmware-stmicroelectronics.pdf
User Manuals | https://www.st.com/resource/en/user_manual/um2840-stm32h7-dualcore-series-safety-manual-stmicroelectronics.pdf
User Manuals | https://www.st.com/resource/en/user_manual/um2331-stm32h7-singlecore-series-safety-manual-stmicroelectronics.pdf
User Manuals | https://www.st.com/resource/en/user_manual/um3252-stm32h7-series-ulcsaiec-607301603351-selftest-library-user-guide-stmicroelectronics.pdf

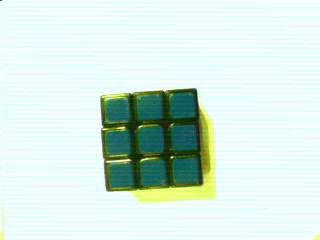
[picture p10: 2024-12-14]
ProjectObelisk_RaspPI_Arduino/Rasp_PI/training_2.png

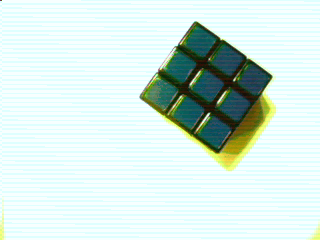
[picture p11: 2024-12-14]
ProjectObelisk_RaspPI_Arduino/Rasp_PI/training_1.png

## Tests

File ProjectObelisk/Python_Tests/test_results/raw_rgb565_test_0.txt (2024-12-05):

(90,91,253) (249,11,167) (11,237,107) (251,59,253) (249,39,11) (237,127,253) (153,11,237) (253,253,227) (195,227,195) (159,191,191) (191,95,95) (95,88,88) (88,112,88) (90,90,253) (251,253,253) (253,153,153) (57,253,141) (13,249,9) (9,237,253) (157,9,253) (153,137,139) (123,219,253) (123,251,253) (253,251,201) (43,253,253) (251,11,253) (227,251,11) (253,249,251) (237,253,253) (155,189,127) (249,139,127) (253,251,11) (253,253,47) (11,127,249) (45,237,127) (249,219,253) (253,249,131) (127,253,251) (45,253,253) (251,11,253) (253,243,253) (253,251,131) (253,253,39) (43,253,249) (219,123,237) (237,237,123) (253,253,25) (253,153,9) (227,11,249) (237,237,123) (123,253,155) (167,11,43) (253,123,249) (173,123,253) (249,249,155) (11,123,251) (251,253,217) (123,253,127) (253,249,153) (139,11,11) (127,253,249) (249,11,123) (253,235,155) (195,155,227) (211,195,195) (191,235,249) (253,249,153) (153,139,9) (231,239,75) (123,123,123) (123,43,123) (237,123,237) (123,253,251) (251,235,251) (203,251,235) (235,195,251) (251,251,251) (253,237,237) (237,251,251) (251,123,253) (251,251,235) (251,195,251) (251,251,251) (251,123,251) (251,251,251) (235,235,13) (253,253,191) (137,9,11) (11,107,43) (237,237,237) (251,9,11) (247,253,237) (237,237,237) (237,251,251) (251,123,11) (25,237,253) (253,251,251) (123,237,237) (237,237,123) (237,123,253) (253,249,153) (11,137,11) (9,9,11) (247,11,139) (237,237,253) (253,253,219) (191,223,123) (139,11,11) (237,253,127) (153,217,11) (11,237,253) (253,253,253) (185,153,139) (11,155,11) (237,123,237) (251,11,253) (253,251,253) (253,25,253) (249,153,157) (253,253,61) (253,9,251) (237,123,123) (251,251,253) (253,249,249) (183,139,11) (237,123,123) (253,253,249) (139,237,237) (123,123,253) (253,253,249) (253,155,155) (11,11,253) (127,253,253) (253,155,155) (11,43,127) (123,253,253) (249,153,139) (123,123,253) (255,253,253) (237,237,237) (251,123,123) (123,105,9) (11,9,141) (9,249,195) (195,235,195) (227,147,251) (203,251,123) (123,11,123) (11,9,9) (141,9,253) (13,253,253) (253,253,253) (235,251,251) (251,251,237) (237,237,237) (123,237,75) (123,107,11) (41,11,9) (191,191,155) (195,195,195) (195,195,251) (251,251,251) (251,251,251) (123,251,251) (9,107,75) (11,9,9) (9,157,13) (157,253,253) (253,237,251) (123,107,11) (9,147,203) (251,123,237) (251,9,251) (9,191,187) (195,251,251) (251,123,107)
(9,9,189) (253,237,237) (237,191,95) (247,115,191) (191,223,191) (241,191,191) (191,243,255) (191,191,241) (247,191,111) (225,229,223) (249,251,173) (237,237,123) (237,237,123) (123,251,139) (251,237,251) (253,251,253) (253,253,253) (253,253,253) (253,9,249) (155,11,11) (107,139,123) (123,123,237) (237,251,43) (11,9,9) (13,13,109) (251,123,251) (9,191,195) (195,235,251) (251,13,45) (237,237,123) (237,237,251) (123,11,29) (237,251,251) (251,123,123) (73,203,251) (251,251,107) (9,237,13) (253,237,237) (251,251,251) (107,237,9) (9,61,237) (253,237,251) (251,123,251) (123,107,9) (13,29,253) (253,237,251) (251,123,237) (75,105,9) (157,247,253) (235,251,251) (251,123,251) (107,9,9) (13,13,253) (237,253,237) (251,123,123) (231,9,9) (25,13,237) (251,251,251) (251,123,123) (107,9,9) (153,45,253) (253,251,251) (251,237,123) (107,105,9) (13,195,195) (251,251,251) (123,237,123) (251,237,45) (237,251,251) (123,9,9) (237,45,251) (237,251,123) (11,9,13) (253,237,237) (237,123,107) (9,247,9) (13,251,123) (237,9,11) (195,251,251) (251,251,13) (191,195,251) (251,123,123) (107,11,13) (45,237,237) (251,251,9) (9,25,253) (195,251,251) (251,251,123) (123,237,11) (247,13,251) (251,13,251) (121,77,251) (251,45,45) (251,109,13) (251,251,73) (13,109,237) (73,45,251) (13,251,127) (131,251,237) (13,251,237) (45,249,13) (251,77,251) (253,13,251) (205,251,251) (13,251,249) (77,45,131) (131,249,205) (251,253,139) (251,237,13) (251,255,131) (251,131,251) (205,251,253) (141,119,179) (253,219,253) (55,253,119) (253,251,237) (119,205,253) (251,237,251) (253,249,253) (253,179,253) (139,253,251) (237,103,131) (253,139,253) (187,13,125) (205,253,163) (253,139,179) (251,253,55) (131,253,251) (205,253,139) (253,139,205) (251,77,253) (13,51,253) (219,253,253) (179,249,139) (237,251,205) (253,251,131) (253,251,253) (253,253,253) (253,139,253) (251,205,253) (39,127,253) (131,253,249) (205,253,219) (221,249,139) (249,13,253) (205,249,51) (253,253,29) (253,55,253) (123,253,249) (155,123,253) (139,63,253) (139,187,249) (139,127,187) (139,253,253) (153,221,253) (253,253,221) (253,231,217) (221,127,253) (119,249,51) (253,253,253) (253,253,253) (155,51,253) (253,143,253) (249,141,253) (255,139,127) (253,3,59) (253,253,157) (253,253,187) (131,253,253) (251,253,127) (185,213,253) (253,249,221) (127,253,255) (51,253,253) (221,253,253) (251,35,253)
(253,139,127) (253,249,137) (253,253,253) (139,253,253) (253,219,51) (253,153,131) (253,253,249) (35,205,253) (249,163,253) (253,157,221) (253,253,139) (51,127,253) (185,221,253) (253,253,205) (253,253,249) (221,127,253) (155,221,253) (249,3,237) (253,253,131) (253,119,137) (253,253,157) (179,253,249) (35,131,255) (253,187,221) (221,253,253) (153,35,253) (255,249,35) (253,253,155) (131,253,55) (219,253,253) (185,35,221) (179,253,13) (253,251,253) (249,179,253) (141,253,249) (253,253,205) (253,139,237) (249,179,253) (139,253,251) (205,253,139) (253,251,205) (249,77,253) (139,253,47) (221,249,131) (253,219,253) (251,131,249) (13,253,251) (253,251,205) (119,139,127) (251,253,251) (179,253,45) (127,251,237) (249,13,253) (219,237,249) (131,253,251) (253,249,253) (253,249,13) (253,249,251) (253,251,115) (253,253,141) (253,251,139) (253,251,237) (249,131,253) (139,127,249) (77,127,251) (237,249,221) (249,131,253) (219,253,249) (139,253,251) (253,249,205) (221,251,131) (253,13,253) (187,29,253) (7,253,155) (51,253,29) (139,253,251) (253,251,253) (253,13,251) (13,251,77) (251,253,249) (249,45,249) (131,251,187) (251,77,45) (249,13,249) (13,251,205) (45,237,13) (251,13,109) (237,45,249) (131,251,77) (251,191,139) (253,77,249) (237,251,205) (249,13,253) (63,253,251) (77,251,139) (249,237,251) (13,111,187) (251,77,109) (205,251,249) (13,249,13) (253,139,237) (253,13,253) (251,253,253) (141,253,251) (127,251,77) (249,131,249) (13,253,139) (253,251,253) (109,253,45) (191,251,253) (13,253,219) (237,251,205) (249,205,249) (203,249,203) (253,139,77) (249,251,253) (45,253,253) (13,127,251) (255,253,205) (253,251,253) (251,205,251) (77,251,59) (253,131,253) (251,253,45) (253,131,251) (221,253,13) (253,249,131) (253,251,237) (139,97,163) (251,205,251) (13,103,77) (251,205,251) (253,187,251) (77,109,253) (251,253,45) (253,139,127) (51,13,13) (249,131,251) (13,251,253) (13,249,13) (251,77,251) (131,249,179) (253,131,249) (13,249,13) (249,77,253) (13,249,131) (249,77,251) (253,13,247) (13,249,13) (249,191,251) (253,127,249) (179,249,187) (251,77,251) (253,131,251) (13,251,77) (219,179,251) (237,251,127) (251,253,13) (247,251,253) (251,253,251) (205,251,237) (139,187,251) (77,249,13) (253,251,205) (253,251,205) (253,13,251) (249,205,253) (139,147,251) (253,109,127) (249,205,251) (187,249,163) (249,13,251) (205,249,205) (251,237,251) (191,203,253) (203,253,139)
(253,13,253) (251,251,77) (251,187,251) (179,249,237) (251,127,251) (253,13,127) (251,253,131) (249,131,251) (205,251,191) (251,253,251) (205,253,251) (237,249,163) (249,13,253) (39,253,203) (253,13,237) (251,127,249) (13,251,13) (251,237,251) (127,251,253) (251,249,187) (251,205,251) (63,249,131) (253,13,253) (13,253,131) (253,203,249) (13,253,45) (253,251,191) (251,205,253) (141,253,45) (253,139,253) (13,253,131) (253,139,253) (251,237,253) (237,249,51) (127,253,179) (253,139,205) (249,205,249) (219,237,45) (191,251,127) (253,139,253) (251,253,247) (131,253,77) (251,13,249) (77,249,13) (253,13,253) (139,253,249) (205,249,163) (249,77,253) (179,99,163) (119,131,253) (29,253,249) (179,253,13) (253,251,249) (13,251,13) (251,13,253) (251,253,253) (13,253,253) (253,249,205) (249,205,249) (203,249,77) (251,77,219) (205,251,127) (253,13,253) (139,253,179) (253,131,249) (13,249,139) (127,251,253) (13,249,205) (253,127,249) (13,253,251) (251,13,45) (249,13,251) (251,77,251) (251,13,45) (251,77,203) (251,77,203) (251,77,251) (251,187,251) (121,123,73) (13,237,237) (121,73,195) (219,251,251) (105,13,109) (237,251,105) (9,13,235) (251,251,73) (13,195,251) (251,73,191) (203,251,237) (251,253,251) (253,13,251) (187,251,237) (109,109,13) (251,13,251) (237,251,237) (251,127,139) (249,179,251) (253,249,253) (251,127,139) (253,45,253) (131,253,13) (253,205,253) (205,119,131) (251,77,251) (191,251,253) (251,253,13) (253,139,127) (139,253,131) (253,131,251) (187,251,237) (139,237,249) (13,253,139) (127,251,203) (249,139,127) (251,187,153) (249,253,249) (205,253,21) (253,251,131) (253,55,131) (253,141,221) (253,13,253) (249,131,253) (253,139,163) (253,253,139) (221,253,187) (205,253,253) (11,221,253) (253,219,253) (253,251,221) (29,253,249) (163,253,251) (141,249,139) (253,13,237) (191,139,237) (249,163,253) (219,253,251) (63,249,131) (253,203,253) (255,139,253) (253,139,253) (139,253,251) (127,249,221) (123,253,153) (221,253,253) (11,221,253) (253,23,253) (253,139,179) (253,251,205) (253,249,139) (253,253,185) (163,253,55) (221,253,153) (163,253,249) (131,253,253) (139,237,253) (155,93,251) (13,119,131) (253,251,237) (251,131,249) (77,253,249) (179,249,251) (237,249,205) (221,251,191) (251,141,253) (13,253,13) (253,13,205) (251,237,249) (237,249,77) (109,191,187) (195,203,249) (13,239,191) (203,249,13) (237,237,203) (119,179,251) (237,13,251) (13,251,249)
(131,251,77) (13,251,237) (45,249,13) (251,237,13) (251,13,251) (13,251,77) (253,139,253) (139,237,47) (253,251,253) (251,77,251) (13,253,139) (253,13,253) (251,205,249) (251,205,251) (163,249,251) (253,249,13) (249,13,253) (139,237,45) (179,249,139) (253,139,253) (187,221,251) (237,61,127) (251,77,249) (13,249,13) (253,141,93) (251,179,253) (13,253,251) (205,45,253) (131,249,205) (253,155,205) (253,13,127) (249,77,249) (205,253,13) (179,253,251) (205,253,251) (253,251,203) (253,219,127) (255,13,253) (249,205,251) (13,253,13) (253,251,253) (13,237,251) (77,251,179) (127,155,253) (249,13,253) (249,253,45) (191,251,237) (251,253,13) (251,253,139) (251,147,251) (13,251,249) (13,251,13) (45,249,13) (251,237,203) (237,13,249) (187,251,253) (251,253,139) (99,131,251) (77,251,253) (13,251,77) (251,253,219) (77,251,187) (249,13,237) (249,13,109) (77,251,249) (235,253,131) (253,13,47) (253,251,237) (45,247,139) (251,237,47) (13,45,249) (131,251,237) (45,237,249) (205,251,205) (251,203,249) (13,249,13) (249,139,253) (131,253,13) (119,179,253) (131,253,45) (253,203,253) (251,249,77) (249,13,249) (131,253,131) (253,131,253) (131,249,13) (253,139,249) (139,253,13) (253,249,221) (253,251,51) (253,55,205) (253,249,139) (253,251,205) (253,139,123) (253,93,253) (251,205,253) (155,237,255) (131,253,155) (221,251,205) (253,155,237) (249,13,253) (13,253,13) (253,251,253) (251,253,251) (187,251,253) (251,205,109) (253,251,163) (253,139,221) (119,131,253) (13,127,219) (253,251,77) (247,77,249) (77,251,77) (45,63,249) (13,251,205) (251,187,251) (253,251,249) (77,249,13) (251,77,251) (179,251,127) (251,253,219) (249,205,125) (253,251,127) (253,139,253) (45,127,249) (251,253,13) (127,251,205) (249,139,253) (13,253,251) (253,249,205) (253,203,253) (139,127,251) (253,251,179) (251,205,253) (13,253,249) (131,253,251) (51,253,205) (237,251,163) (253,13,127) (251,205,253) (139,253,249) (205,193,203) (127,139,253) (13,253,45) (253,251,255) (251,205,249) (205,249,13) (249,13,253) (13,253,13) (253,13,253) (39,237,251) (77,251,205) (247,13,249) (13,253,13) (253,139,253) (251,253,251) (77,45,13) (249,13,253) (251,253,13) (253,45,237) (249,139,253) (253,253,137) (131,253,253) (155,131,253) (253,139,123) (253,219,253) (55,163,253) (205,221,249) (139,253,251) (127,253,205) (253,13,247) (251,205,249) (139,253,251) (237,155,179) (249,139,253) (139,127,251)
(179,253,139) (253,251,187) (251,131,253) (251,127,249) (205,255,139) (253,253,237) (253,139,253) (253,155,131) (253,139,253) (63,23,253) (253,139,127) (249,205,131) (249,139,237) (45,253,251) (253,253,77) (253,139,253) (219,253,45) (253,13,253) (251,237,119) (205,249,131) (249,179,249) (131,251,205) (251,13,249) (13,253,251) (237,251,179) (187,29,249) (13,253,219) (253,251,253) (251,237,251) (255,251,205) (249,139,237) (55,139,253) (249,205,249) (141,253,251) (253,253,205) (251,205,119) (203,253,253) (237,251,127) (251,237,251) (205,251,191) (251,253,39) (205,249,219) (237,119,141) (253,45,249) (13,249,13) (119,139,237) (249,179,253) (251,255,253) (139,237,249) (35,253,251) (237,61,191) (251,237,155) (253,253,249) (131,253,55) (157,253,253) (31,253,253) (225,139,253) (253,253,131) (255,249,205) (253,253,31) (237,253,253) (221,255,253) (221,253,249) (237,253,249) (141,253,119) (139,253,253) (253,205,253) (253,141,253) (249,139,249) (13,249,139) (253,249,131) (59,253,155) (131,127,251) (253,251,187) (253,139,253) (139,187,253) (139,187,253) (115,253,139) (253,253,13) (253,253,253) (115,253,253) (251,205,253) (139,237,249) (141,127,249) (205,253,249) (127,253,13) (253,249,205) (253,29,123) (253,251,205) (249,179,253) (163,255,249) (205,253,249) (131,127,253) (131,127,249) (205,253,249) (139,237,253) (251,59,253) (153,139,253) (21,221,253) (139,221,127) (253,163,253) (249,205,115) (253,253,249) (139,253,253) (253,139,253) (253,253,131) (253,247,139) (205,253,249) (205,253,253) (155,51,253) (253,219,253) (253,251,51) (253,251,51) (253,249,131) (253,23,139) (127,253,139) (253,253,139) (127,253,139) (253,253,29) (253,249,29) (253,253,221) (253,253,139) (123,253,249) (143,127,249) (139,253,253) (131,253,249) (131,253,249) (205,253,251) (221,253,141) (223,253,249) (131,253,119) (139,131,253) (139,253,253) (137,63,253) (249,179,253) (21,139,253) (253,155,221) (127,249,205) (253,251,139) (253,139,253) (249,51,253) (251,77,253) (251,77,253) (249,237,119) (139,253,251) (77,251,187) (251,77,251) (205,251,237) (251,77,251) (205,249,77) (251,127,251) (205,249,179) (249,203,253) (251,253,139) (253,203,253) (139,253,139) (253,251,237) (251,237,251) (237,253,141) (127,251,131) (249,251,253) (61,237,249) (139,253,131) (253,109,109) (131,251,77) (251,205,55) (131,253,45) (127,251,253) (253,139,253) (249,179,249) (13,253,13) (253,13,253) (251,179,249) (13,253,13) (253,45,237) (251,127,251)
(237,251,253) (139,249,13) (249,77,251) (205,251,187) (249,77,247) (205,249,205) (249,77,13) (251,195,235) (251,77,203) (251,237,251) (251,109,45) (237,251,251) (251,105,13) (237,247,13) (251,251,237) (45,237,255) (195,251,77) (45,249,219) (249,131,251) (253,203,253) (187,251,205) (245,237,251) (253,131,249) (13,251,109) (187,251,249) (77,109,237) (251,251,125) (13,253,13) (251,187,251) (237,45,249) (167,251,131) (251,237,109) (253,139,237) (203,251,77) (251,249,253) (251,13,237) (249,13,251) (77,109,253) (131,249,205) (251,237,251) (191,251,179) (249,131,251) (205,249,77) (249,205,253) (13,221,251) (205,249,13) (249,205,253) (139,253,13) (253,251,253) (251,253,251) (237,251,253) (251,205,119) (77,251,13) (251,127,251) (179,251,205) (253,251,237) (251,237,249) (13,249,139) (253,45,237) (251,205,249) (13,249,13) (119,23,205) (253,139,253) (249,163,253) (13,253,249) (253,253,163) (127,139,253) (249,253,249) (237,249,237) (119,131,249) (13,249,139) (127,131,249) (179,249,205) (109,237,251) (253,251,77) (249,163,253) (77,249,13) (251,77,249) (205,251,13) (251,77,251) (127,251,253) (249,59,253) (13,253,249) (205,253,219) (253,251,221) (249,13,237) (251,221,253) (139,253,253) (205,253,251) (179,253,205) (221,253,133) (253,253,139) (131,253,255) (253,253,139) (253,155,139) (253,251,51) (253,139,237) (249,163,253) (139,253,251) (77,249,219) (127,249,205) (253,29,205) (249,139,253) (251,205,249) (131,253,139) (253,55,205) (127,139,191) (251,141,253) (139,127,249) (51,253,13) (253,251,131) (253,13,253) (249,179,253) (139,253,251) (205,253,15) (253,253,163) (253,251,253) (249,205,253) (251,127,249) (13,253,251) (127,249,13) (253,251,253) (249,205,237) (251,187,249) (251,253,251) (237,253,179) (127,251,205) (249,139,253) (55,205,253) (139,253,249) (205,253,13) (253,251,205) (253,139,253) (249,205,253) (13,127,251) (187,249,139) (253,13,205) (249,13,253) (61,127,253) (141,253,251) (51,253,139) (237,251,205) (253,13,253) (251,205,227) (139,253,251) (237,249,77) (253,251,205) (249,139,127) (251,253,253) (29,237,253) (251,253,253) (139,123,253) (157,139,253) (23,123,253) (251,131,253) (253,141,253) (249,93,253) (253,13,253) (253,115,253) (253,137,221) (127,253,253) (221,115,253) (23,215,131) (253,253,221) (253,249,35) (253,253,157) (127,253,139) (253,253,221) (253,119,139) (253,255,155) (221,253,249) (131,253,249) (131,253,55) (131,127,249) (139,253,249) (139,127,253)
(139,253,253) (139,237,253) (253,155,253) (253,139,221) (253,251,115) (253,29,179) (249,13,253) (251,205,125) (221,253,137) (139,253,253) (139,255,255) (51,253,251) (253,253,13) (253,251,205) (253,139,253) (251,203,249) (77,249,203) (253,155,29) (253,249,139) (253,251,237) (251,13,249) (131,249,131) (253,13,253) (55,253,251) (205,249,179) (249,77,249) (131,249,139) (253,15,237) (251,127,249) (205,253,131) (249,13,253) (13,253,139) (237,139,205) (39,237,249) (205,253,13) (253,45,253) (251,205,55) (205,249,205) (249,77,253) (139,253,45) (127,251,253) (251,179,249) (77,249,13) (127,139,253) (45,253,251) (237,249,205) (119,13,231) (203,253,139) (253,139,127) (251,205,251) (179,253,29) (127,249,115) (253,251,205) (249,219,253) (219,127,249) (77,253,13) (253,251,163) (249,13,127) (249,205,249) (139,253,139) (123,253,13) (253,55,237) (251,131,231) (203,253,13) (253,139,237) (29,253,249) (139,253,249) (131,237,13) (253,131,253) (219,253,249) (205,253,13) (253,29,237) (253,127,251) (187,251,237) (119,77,249) (147,251,205) (249,13,251) (131,251,77) (251,237,253) (131,127,251) (253,251,253) (139,127,251) (253,249,253) (249,251,253) (253,131,253) (21,163,253) (251,187,249) (139,255,253) (255,249,215) (163,253,253) (249,221,51) (253,153,139) (127,127,153) (139,253,127) (217,131,63) (249,139,127) (231,139,59) (127,253,163) (127,253,139) (253,205,253) (155,205,251) (179,253,15) (253,219,253) (187,29,253) (251,205,253) (13,253,13) (253,13,253) (203,253,139) (253,249,139) (253,255,131) (249,237,253) (203,127,251) (253,139,253) (13,127,251) (253,139,13) (253,235,253) (251,253,47) (205,249,237) (251,237,45) (253,249,13) (253,139,253) (139,253,251) (253,13,253) (251,253,251) (237,251,77) (251,205,251) (13,251,163) (253,131,253) (13,127,163) (249,77,249) (205,253,251) (179,253,139) (253,251,77) (203,253,251) (253,13,127) (249,139,253) (39,127,251) (249,139,255) (249,205,253) (251,205,253) (251,51,253) (251,237,253) (55,139,253) (251,221,127) (251,35,127) (253,187,205) (253,249,3) (131,253,155) (205,127,139) (127,253,139) (253,249,143) (253,253,139) (253,253,139) (253,119,139) (253,29,63) (253,13,221) (253,251,205) (127,251,255) (191,139,221) (253,251,253) (253,251,253) (251,253,251) (205,253,139) (51,127,253) (221,163,253) (23,127,253) (23,221,253) (253,253,253) (151,255,221) (253,253,253) (253,253,139) (253,253,253) (153,139,253) (253,253,253) (215,115,253) (253,253,139)
(123,253,253) (189,9,221) (253,253,137) (221,127,253) (251,141,253) (253,135,253) (249,249,51) (253,249,139) (253,253,253) (221,253,55) (163,127,253) (251,253,127) (155,237,253) (237,251,205) (249,205,253) (13,253,251) (237,119,115) (191,131,127) (251,237,251) (77,249,205) (119,13,249) (205,127,251) (187,253,205) (249,139,253) (163,253,15) (253,251,237) (253,13,253) (219,253,61) (251,253,249) (251,253,55) (237,253,139) (253,251,205) (249,205,253) (139,253,251) (77,249,13) (253,251,127) (253,131,249) (13,253,249) (253,249,205) (249,131,253) (13,253,55) (205,249,205) (253,13,127) (251,253,39) (127,249,205) (249,205,249) (139,253,219) (205,249,131) (249,139,253) (15,77,253) (77,253,203) (253,251,237) (249,139,253) (251,131,251) (139,253,251) (237,251,59) (253,13,253) (251,127,249) (179,253,205) (227,219,253) (251,205,249) (77,253,13) (253,187,15) (249,139,253) (251,127,249) (205,103,139) (253,13,253) (249,131,253) (253,51,253) (249,205,253) (61,187,249) (205,249,251) (253,251,205) (253,139,249) (253,205,253) (45,123,251) (77,253,219) (205,253,45) (253,249,51) (253,249,13) (127,131,253) (219,205,251) (131,127,219) (179,249,139) (253,45,253) (249,77,253) (29,253,249) (31,253,39) (205,249,205) (253,203,253) (45,253,249) (51,127,251) (205,253,155) (187,249,255) (253,251,205) (249,139,253) (251,131,253) (139,253,251) (139,123,253) (253,23,127) (253,205,253) (253,187,221) (187,193,201) (35,127,127) (155,221,253) (251,179,249) (13,253,219) (205,249,139) (253,155,237) (253,139,253) (251,205,253) (13,253,251) (221,249,13) (253,251,205) (249,13,127) (251,205,253) (131,253,249) (179,253,139) (237,249,205) (127,251,109) (13,249,205) (231,205,249) (47,187,249) (139,253,21) (139,253,249) (139,253,253) (251,253,249) (163,253,253) (155,251,255) (253,253,157) (221,253,253) (253,139,163) (127,253,139) (115,253,29) (253,253,253) (155,205,253) (249,205,255) (251,123,253) (53,131,127) (249,139,253) (55,131,253) (249,163,253) (249,127,253) (251,253,253) (139,63,249) (221,253,251) (253,253,251) (221,253,31) (253,253,255) (253,249,139) (253,249,205) (253,255,253) (253,249,123) (253,155,123) (253,249,131) (127,157,29) (253,139,205) (249,139,253) (253,29,253) (253,219,179) (249,29,253) (155,139,253) (251,237,249) (139,253,139) (237,249,205) (253,253,155) (221,253,23) (205,253,131) (253,251,205) (249,15,127) (249,93,253) (13,253,251) (205,253,13) (253,251,127) (253,205,127) (249,141,253)
(219,253,249) (23,253,119) (131,253,139) (253,253,131) (253,249,151) (237,253,139) (253,253,139) (237,253,13) (253,13,253) (251,77,249) (77,253,221) (249,205,255) (131,255,139) (253,55,253) (249,205,249) (55,231,251) (253,251,237) (251,179,249) (237,251,205) (253,13,249) (13,237,251) (191,249,77) (251,237,251) (205,249,51) (253,249,131) (253,13,253) (251,179,253) (13,253,139) (253,251,253) (253,253,251) (237,139,253) (139,237,251) (237,251,253) (45,253,13) (237,251,77) (251,251,13) (251,253,13) (237,77,139) (13,13,237) (249,13,251) (205,251,255) (251,253,131) (249,13,249) (251,249,13) (249,131,249) (191,251,237) (139,77,131) (249,131,251) (139,253,219) (237,251,253) (249,77,139) (253,251,237) (249,179,251) (205,251,191) (251,253,251) (249,195,203) (251,237,13) (251,249,13) (251,251,13) (235,251,13) (109,253,13) (251,255,139) (251,77,203) (251,13,251) (251,13,203) (251,13,13) (251,77,131) (251,249,13) (45,251,13) (251,13,251) (77,13,253) (13,251,255) (203,249,163) (249,139,249) (77,249,13) (203,253,131) (253,13,247) (219,249,13) (251,237,251) (249,131,251) (13,239,13) (251,253,251) (253,163,251) (77,251,249) (131,251,77) (45,253,131) (251,237,249) (253,235,249) (131,251,237) (119,205,249) (205,251,221) (249,13,253) (47,253,251) (253,249,205) (253,55,253) (253,13,253) (251,253,249) (13,253,115) (131,251,131) (253,251,237) (253,131,253) (139,253,251) (205,253,251) (163,253,15) (253,249,139) (249,139,127) (249,205,253) (155,237,249) (163,253,11) (29,249,29) (205,253,131) (253,251,63) (249,13,253) (251,253,253) (23,191,253) (35,187,249) (131,253,253) (251,205,253) (251,205,127) (249,131,253) (153,249,253) (249,139,253) (253,143,253) (249,139,253) (251,131,253) (155,205,253) (139,205,253) (251,253,187) (179,119,139) (253,253,253) (141,253,253) (23,131,253) (23,221,253) (253,155,253) (253,155,205) (253,151,215) (123,253,253) (153,221,253) (253,249,221) (127,253,139) (179,253,251) (179,249,179) (253,13,253) (55,221,249) (179,253,139) (253,251,205) (253,251,237) (251,205,249) (51,253,139) (191,251,205) (249,131,251) (253,45,249) (13,251,13) (251,205,251) (237,251,253) (251,253,13) (247,179,251) (255,251,253) (13,251,77) (251,253,45) (249,131,251) (77,251,237) (13,231,187) (251,237,45) (253,13,251) (163,249,13) (253,13,251) (131,249,77) (251,255,251) (253,13,249) (13,251,237) (251,237,13) (249,77,251) (205,251,255) (139,253,13) (253,13,249)
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

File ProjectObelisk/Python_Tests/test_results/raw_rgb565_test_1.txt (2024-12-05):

(249,55,139) (237,59,127) (253,253,195) (13,25,141) (11,123,237) (237,123,253) (251,253,123) (253,253,25) (253,219,39) (139,123,253) (253,249,235) (155,173,123) (127,253,227) (203,11,11) (253,253,253) (253,253,253) (253,153,249) (9,247,11) (11,43,123) (123,237,237) (237,123,123) (253,253,237) (123,251,251) (253,253,253) (253,253,171) (155,11,11) (75,253,9) (61,253,253) (253,189,195) (251,251,251) (251,235,251) (251,123,253) (253,253,253) (253,237,253) (253,249,217) (155,9,11) (43,123,123) (237,253,237) (251,107,123) (107,43,237) (123,253,253) (253,253,253) (253,253,253) (253,253,195) (191,251,249) (153,217,11) (11,183,11) (11,11,123) (237,251,123) (237,251,107) (123,75,11) (237,123,253) (253,235,195) (195,251,251) (251,75,107) (9,25,131) (251,251,251) (123,237,107) (231,9,11) (11,231,11) (11,9,11) (157,141,25) (13,25,237) (253,253,195) (195,195,147) (251,237,251) (251,251,75) (9,173,9) (235,253,253) (217,11,11) (11,251,123) (231,9,9) (137,183,9) (237,253,253) (251,195,251) (235,249,153) (175,123,123) (251,251,253) (251,251,251) (251,251,123) (253,253,253) (153,25,9) (25,183,11) (11,239,231) (11,237,237) (237,237,255) (253,253,253) (253,249,217) (9,217,239) (11,11,237) (123,237,253) (251,123,251) (123,123,123) (123,123,251) (251,251,251) (123,237,251) (123,253,251) (251,253,253) (253,237,253) (253,253,249) (253,191,203) (195,235,195) (251,251,251) (251,131,123) (253,253,251) (251,251,251) (251,123,251) (251,251,251) (251,253,237) (237,237,237) (251,251,253) (253,253,253) (253,253,253) (251,251,251) (253,253,123) (195,235,235) (235,195,195) (235,235,195) (195,227,13) (237,251,251) (251,123,123) (237,123,237) (237,237,123) (237,237,123) (239,43,123) (123,11,43) (123,11,9) (9,9,9) (25,9,237) (253,253,253) (253,253,237) (251,253,235) (251,251,251) (251,251,73) (13,13,237) (237,237,251) (251,105,13) (247,251,251) (251,9,9) (13,45,123) (105,13,45) (251,191,195) (203,251,249) (13,195,251) (251,251,251) (13,45,45) (249,105,235) (251,249,13) (203,251,251) (251,251,107) (9,13,253) (251,251,251) (123,73,237) (147,251,251) (251,251,77) (13,237,251) (239,191,203) (251,107,45) (237,239,255) (195,251,251) (251,77,251) (251,191,195) (251,249,13) (237,249,251) (203,251,109) (13,237,249) (47,251,233) (13,251,77) (13,251,147) (131,251,237) (173,251,249) (77,131,251) (73,13,45) (251,73,13) (251,251,191) (131,251,251)
(105,13,203) (251,233,13) (251,251,13) (203,251,123) (255,203,251) (251,77,251) (251,73,13) (251,251,13) (131,251,251) (13,13,251) (77,203,251) (77,13,249) (13,179,249) (249,45,237) (251,123,9) (203,155,235) (251,237,123) (251,9,9) (187,235,235) (251,251,251) (123,123,107) (9,13,237) (237,251,251) (251,13,247) (13,237,45) (251,251,123) (253,251,251) (251,203,123) (237,123,123) (107,9,9) (237,61,253) (253,237,251) (251,191,131) (131,251,251) (251,123,73) (237,251,251) (123,237,13) (237,237,249) (237,237,251) (251,77,13) (195,251,123) (123,251,251) (123,237,237) (75,11,9) (9,157,9) (29,251,253) (253,237,237) (237,237,123) (123,251,123) (237,237,11) (11,9,157) (9,13,45) (173,13,195) (195,195,203) (251,251,251) (251,123,237) (251,141,11) (9,191,191) (203,191,235) (13,253,167) (13,137,237) (11,237,11) (237,11,123) (11,237,237) (253,253,253) (249,153,175) (239,59,237) (251,251,131) (251,253,235) (251,235,235) (235,123,237) (251,73,107) (9,11,11) (11,137,157) (253,13,9) (153,191,191) (191,131,195) (195,195,195) (187,251,195) (195,219,191) (195,155,187) (219,203,191) (155,203,195) (9,13,249) (9,9,9) (9,11,11) (247,229,11) (11,139,11) (11,11,11) (11,123,11) (123,123,123) (123,77,45) (251,251,251) (251,123,237) (173,131,251) (123,237,141) (183,253,251) (251,73,13) (237,231,105) (45,237,251) (73,13,251) (107,13,235) (251,13,187) (251,249,109) (13,237,105) (13,109,237) (249,13,251) (251,121,13) (109,251,105) (155,203,251) (251,77,173) (251,105,45) (251,251,77) (131,251,251) (13,45,251) (249,179,251) (253,13,251) (109,139,249) (13,249,131) (249,205,39) (253,139,249) (205,119,77) (109,141,249) (13,251,13) (251,77,131) (251,13,251) (253,13,249) (13,109,253) (45,119,235) (251,187,251) (237,109,253) (45,249,13) (251,131,251) (131,251,13) (249,191,251) (253,251,249) (131,97,131) (251,141,249) (131,249,13) (249,205,249) (251,13,251) (127,131,251) (253,131,251) (253,13,251) (237,235,249) (13,45,249) (139,253,13) (249,253,13) (251,237,251) (205,249,187) (249,231,253) (237,251,253) (139,253,13) (247,251,249) (13,251,205) (253,131,253) (251,127,251) (237,251,249) (179,251,237) (139,253,251) (77,249,141) (249,13,253) (163,249,13) (253,13,253) (251,205,253) (139,253,13) (29,251,131) (249,13,253) (155,127,251) (253,251,253) (253,13,253) (249,131,253) (13,253,251) (205,253,249) (51,253,139) (253,45,237)
(29,77,119) (163,253,139) (253,251,127) (249,115,131) (249,139,253) (255,253,253) (205,253,139) (253,251,77) (249,205,249) (13,253,139) (13,251,77) (253,131,253) (139,253,13) (253,13,253) (45,187,253) (251,51,253) (251,253,117) (253,251,253) (45,237,249) (77,253,139) (249,205,249) (253,253,253) (155,179,127) (251,253,251) (253,251,237) (251,237,253) (253,179,253) (249,253,253) (253,221,127) (253,219,253) (139,237,253) (205,251,77) (251,187,251) (251,249,131) (253,139,191) (139,253,249) (253,109,147) (251,77,251) (237,251,249) (163,251,253) (13,253,13) (253,205,253) (13,253,13) (251,131,249) (77,249,205) (249,237,109) (237,251,191) (251,77,251) (131,251,205) (249,131,251) (127,251,253) (251,191,221) (187,251,191) (251,253,253) (251,141,253) (247,251,123) (253,119,131) (59,253,251) (253,253,251) (77,119,205) (249,13,253) (187,139,127) (253,249,149) (253,253,253) (221,221,253) (55,35,127) (253,139,237) (253,23,131) (253,249,139) (253,253,251) (221,253,29) (59,253,23) (35,253,253) (249,131,253) (55,253,253) (253,23,221) (253,247,251) (35,127,251) (221,253,253) (205,127,253) (139,253,253) (131,253,141) (253,139,127) (253,139,123) (253,185,221) (253,253,139) (123,127,193) (157,253,253) (139,253,253) (139,123,253) (139,51,253) (253,249,253) (249,139,253) (199,157,3) (35,253,253) (253,43,221) (253,249,29) (255,127,153) (131,253,251) (51,127,253) (51,253,249) (205,253,253) (139,253,253) (163,253,253) (253,51,253) (21,205,127) (249,205,253) (251,253,253) (139,221,253) (253,249,221) (127,253,253) (35,253,253) (153,205,253) (253,253,249) (139,253,253) (253,123,253) (253,221,59) (249,253,205) (249,139,187) (231,139,253) (251,179,253) (131,253,141) (253,253,139) (253,251,127) (249,179,225) (131,249,139) (253,139,253) (45,127,251) (237,249,253) (251,205,249) (205,253,155) (237,249,179) (253,139,131) (249,205,253) (139,253,155) (237,249,205) (249,131,253) (203,127,251) (77,251,205) (249,13,249) (131,253,13) (253,251,205) (253,251,179) (247,139,131) (253,155,131) (253,249,237) (253,251,127) (253,251,179) (253,137,127) (249,205,249) (139,127,251) (205,253,163) (253,155,221) (253,139,131) (253,249,221) (253,253,187) (131,253,253) (155,253,253) (253,139,253) (253,23,131) (127,251,127) (249,221,253) (139,191,249) (29,221,231) (139,63,249) (253,251,205) (221,123,253) (13,253,13) (127,251,237) (253,205,249) (13,253,131) (253,45,253) (251,191,251) (237,249,77) (119,131,253) (139,253,45)
(253,251,191) (251,131,249) (77,253,31) (179,253,251) (253,249,127) (155,179,249) (139,253,251) (253,249,205) (253,13,253) (131,249,253) (123,253,21) (205,253,13) (253,249,253) (119,13,249) (109,251,249) (13,109,253) (45,249,163) (251,237,45) (125,13,249) (191,251,253) (13,247,191) (251,251,77) (251,109,13) (249,187,251) (249,77,251) (249,77,251) (253,131,249) (203,253,13) (253,139,253) (249,253,251) (253,251,253) (13,237,119) (187,253,13) (253,45,205) (251,253,251) (77,251,253) (251,249,131) (251,77,13) (109,251,251) (13,45,237) (239,191,147) (251,251,249) (13,45,237) (251,13,13) (237,251,73) (13,45,237) (251,191,139) (121,233,195) (251,249,77) (187,251,77) (247,45,237) (239,191,195) (251,109,13) (251,237,203) (251,77,203) (251,77,235) (251,77,45) (251,13,251) (249,77,45) (237,13,13) (45,251,77) (109,237,249) (251,251,105) (131,251,251) (13,13,251) (251,191,195) (251,249,13) (251,249,13) (251,237,139) (253,131,251) (13,251,251) (13,251,251) (105,13,251) (105,131,251) (253,13,237) (251,205,251) (249,13,237) (251,205,45) (13,13,77) (39,77,45) (127,155,205) (249,63,251) (77,45,253) (251,249,13) (251,13,237) (205,251,253) (131,249,77) (251,191,251) (253,13,249) (131,249,77) (109,253,195) (203,253,13) (251,237,45) (249,131,251) (253,203,251) (13,119,77) (249,131,119) (195,251,237) (147,251,237) (139,249,77) (237,253,203) (251,77,195) (251,251,249) (77,45,109) (255,131,251) (251,13,237) (249,77,251) (249,13,195) (251,251,237) (237,237,231) (13,45,237) (251,251,73) (13,237,251) (251,13,251) (253,13,109) (233,13,109) (251,237,13) (237,109,109) (251,13,251) (251,77,139) (13,13,251) (77,45,251) (77,203,251) (253,45,251) (77,155,205) (251,237,251) (77,251,237) (139,127,249) (237,251,237) (253,251,237) (253,251,237) (251,237,13) (249,77,251) (13,109,77) (109,253,131) (127,251,253) (251,205,249) (163,253,131) (253,203,253) (251,77,205) (187,251,131) (253,143,127) (251,13,253) (13,253,13) (191,219,205) (249,221,253) (13,253,249) (253,251,205) (249,23,249) (45,205,251) (253,249,251) (253,139,253) (251,131,253) (187,205,249) (139,253,253) (205,253,187) (253,13,253) (77,253,251) (237,249,131) (253,139,93) (45,237,249) (179,249,179) (253,13,255) (139,249,13) (237,249,251) (205,253,15) (253,251,253) (251,253,251) (253,39,131) (249,13,249) (77,249,249) (77,253,251) (205,253,55) (205,127,249) (221,253,249) (205,253,141)
(253,251,237) (249,139,253) (187,123,253) (135,131,249) (13,253,139) (179,253,139) (253,55,253) (253,205,253) (55,131,253) (251,253,251) (127,249,205) (253,251,237) (255,131,253) (139,253,249) (237,249,77) (127,139,127) (253,13,253) (55,179,253) (253,59,253) (203,253,251) (179,249,13) (253,251,127) (253,139,253) (251,205,253) (13,253,23) (35,127,249) (251,253,249) (139,59,253) (135,221,253) (243,29,253) (253,131,253) (185,213,123) (253,23,221) (253,253,205) (127,253,139) (19,127,249) (163,253,205) (253,139,253) (251,205,253) (45,127,251) (123,253,55) (253,249,205) (119,139,253) (251,237,119) (205,253,139) (255,139,77) (249,205,253) (29,253,13) (237,249,205) (249,13,253) (253,179,253) (13,253,253) (205,127,249) (29,253,251) (51,253,249) (131,253,251) (253,253,141) (127,219,205) (251,221,253) (205,249,13) (253,251,179) (249,39,127) (251,179,253) (249,253,253) (205,253,155) (179,249,203) (253,251,253) (249,139,253) (251,237,249) (205,253,7) (253,251,253) (249,205,253) (251,123,253) (249,131,127) (249,131,253) (251,221,253) (141,127,249) (253,249,141) (127,139,237) (253,131,253) (251,127,251) (127,251,237) (249,13,249) (13,249,13) (249,131,249) (131,253,203) (253,251,253) (251,253,251) (127,251,187) (251,77,251) (205,119,77) (249,131,253) (139,253,131) (249,139,253) (13,253,13) (253,251,127) (219,253,251) (253,251,253) (251,237,251) (13,251,139) (253,253,249) (221,253,249) (29,253,253) (29,253,253) (77,253,13) (253,13,249) (13,249,163) (253,45,253) (55,131,249) (77,45,253) (131,253,205) (253,251,127) (253,205,253) (45,187,219) (127,251,205) (251,179,253) (139,253,13) (253,13,77) (45,205,251) (77,251,205) (253,237,119) (187,251,205) (253,141,237) (55,131,249) (155,179,253) (139,237,251) (147,249,179) (253,251,253) (117,253,253) (251,253,119) (127,249,141) (249,139,249) (139,253,203) (253,251,127) (249,131,253) (139,253,251) (249,139,253) (219,253,249) (205,253,131) (249,13,253) (253,237,253) (13,253,251) (59,253,205) (249,13,253) (163,253,13) (253,13,247) (251,253,219) (253,13,253) (205,253,131) (253,77,249) (251,253,251) (237,249,205) (249,205,253) (155,253,253) (13,253,119) (179,253,139) (93,249,131) (253,139,253) (249,131,253) (139,253,251) (253,253,139) (237,253,251) (221,253,203) (249,13,253) (251,127,255) (139,253,251) (221,251,115) (187,139,127) (249,13,253) (139,139,127) (139,253,251) (51,253,203) (253,251,51) (253,23,253) (251,127,251) (253,249,205)
(253,13,253) (139,253,249) (163,253,23) (237,253,139) (127,253,237) (253,31,123) (253,255,205) (253,253,151) (253,249,139) (253,253,137) (35,253,253) (139,253,253) (253,205,127) (253,139,253) (249,13,249) (13,127,219) (253,249,205) (253,55,141) (127,249,93) (251,205,253) (205,253,251) (253,251,77) (251,205,251) (23,253,249) (93,253,249) (139,205,119) (141,221,253) (23,205,255) (253,185,157) (253,253,185) (131,253,253) (139,253,253) (249,205,253) (253,151,253) (253,185,131) (253,253,139) (127,253,249) (131,253,255) (155,221,127) (253,191,177) (239,127,153) (221,253,253) (221,253,253) (155,221,253) (249,139,253) (253,137,35) (127,127,249) (163,253,253) (139,253,221) (7,253,253) (251,215,253) (253,151,139) (127,253,253) (139,221,253) (253,253,139) (253,127,139) (35,127,253) (155,253,253) (139,115,127) (253,139,221) (253,247,155) (221,253,11) (23,237,253) (23,163,253) (249,201,253) (15,253,253) (35,253,155) (221,253,11) (251,253,251) (221,253,219) (127,249,29) (251,13,127) (139,253,249) (131,249,205) (253,251,253) (249,179,253) (251,253,249) (205,255,131) (127,251,221) (249,131,253) (249,123,253) (139,253,119) (205,253,219) (237,251,163) (253,13,253) (251,205,249) (131,253,139) (253,251,205) (119,141,253) (155,221,185) (249,205,253) (253,139,253) (253,155,205) (253,7,253) (127,251,179) (253,251,253) (61,237,249) (13,255,251) (187,249,93) (253,253,51) (253,139,253) (63,179,253) (13,253,139) (127,253,35) (205,253,155) (205,103,203) (253,139,253) (251,127,249) (45,205,249) (77,253,13) (253,13,253) (45,205,249) (139,237,251) (77,249,131) (253,249,127) (249,13,253) (139,253,251) (187,249,131) (253,139,255) (127,253,139) (253,253,223) (253,249,139) (3,127,253) (29,205,249) (139,253,13) (131,253,139) (131,253,23) (131,253,221) (131,253,253) (51,253,253) (131,253,253) (155,221,127) (249,51,253) (253,179,253) (249,131,253) (249,139,127) (253,131,253) (251,139,253) (249,205,253) (249,253,249) (237,251,77) (251,205,119) (39,131,253) (155,179,253) (77,251,127) (251,237,249) (221,253,253) (139,205,253) (255,253,253) (249,237,253) (23,131,253) (139,221,249) (139,253,249) (163,127,249) (179,253,139) (253,251,139) (253,251,179) (249,5,127) (251,253,251) (253,251,187) (249,13,253) (45,253,249) (237,253,131) (253,251,253) (249,77,251) (205,251,237) (251,253,253) (13,253,139) (205,251,205) (251,13,251) (191,251,237) (251,233,13) (251,249,77) (251,249,13) (251,249,13) (251,249,179)
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

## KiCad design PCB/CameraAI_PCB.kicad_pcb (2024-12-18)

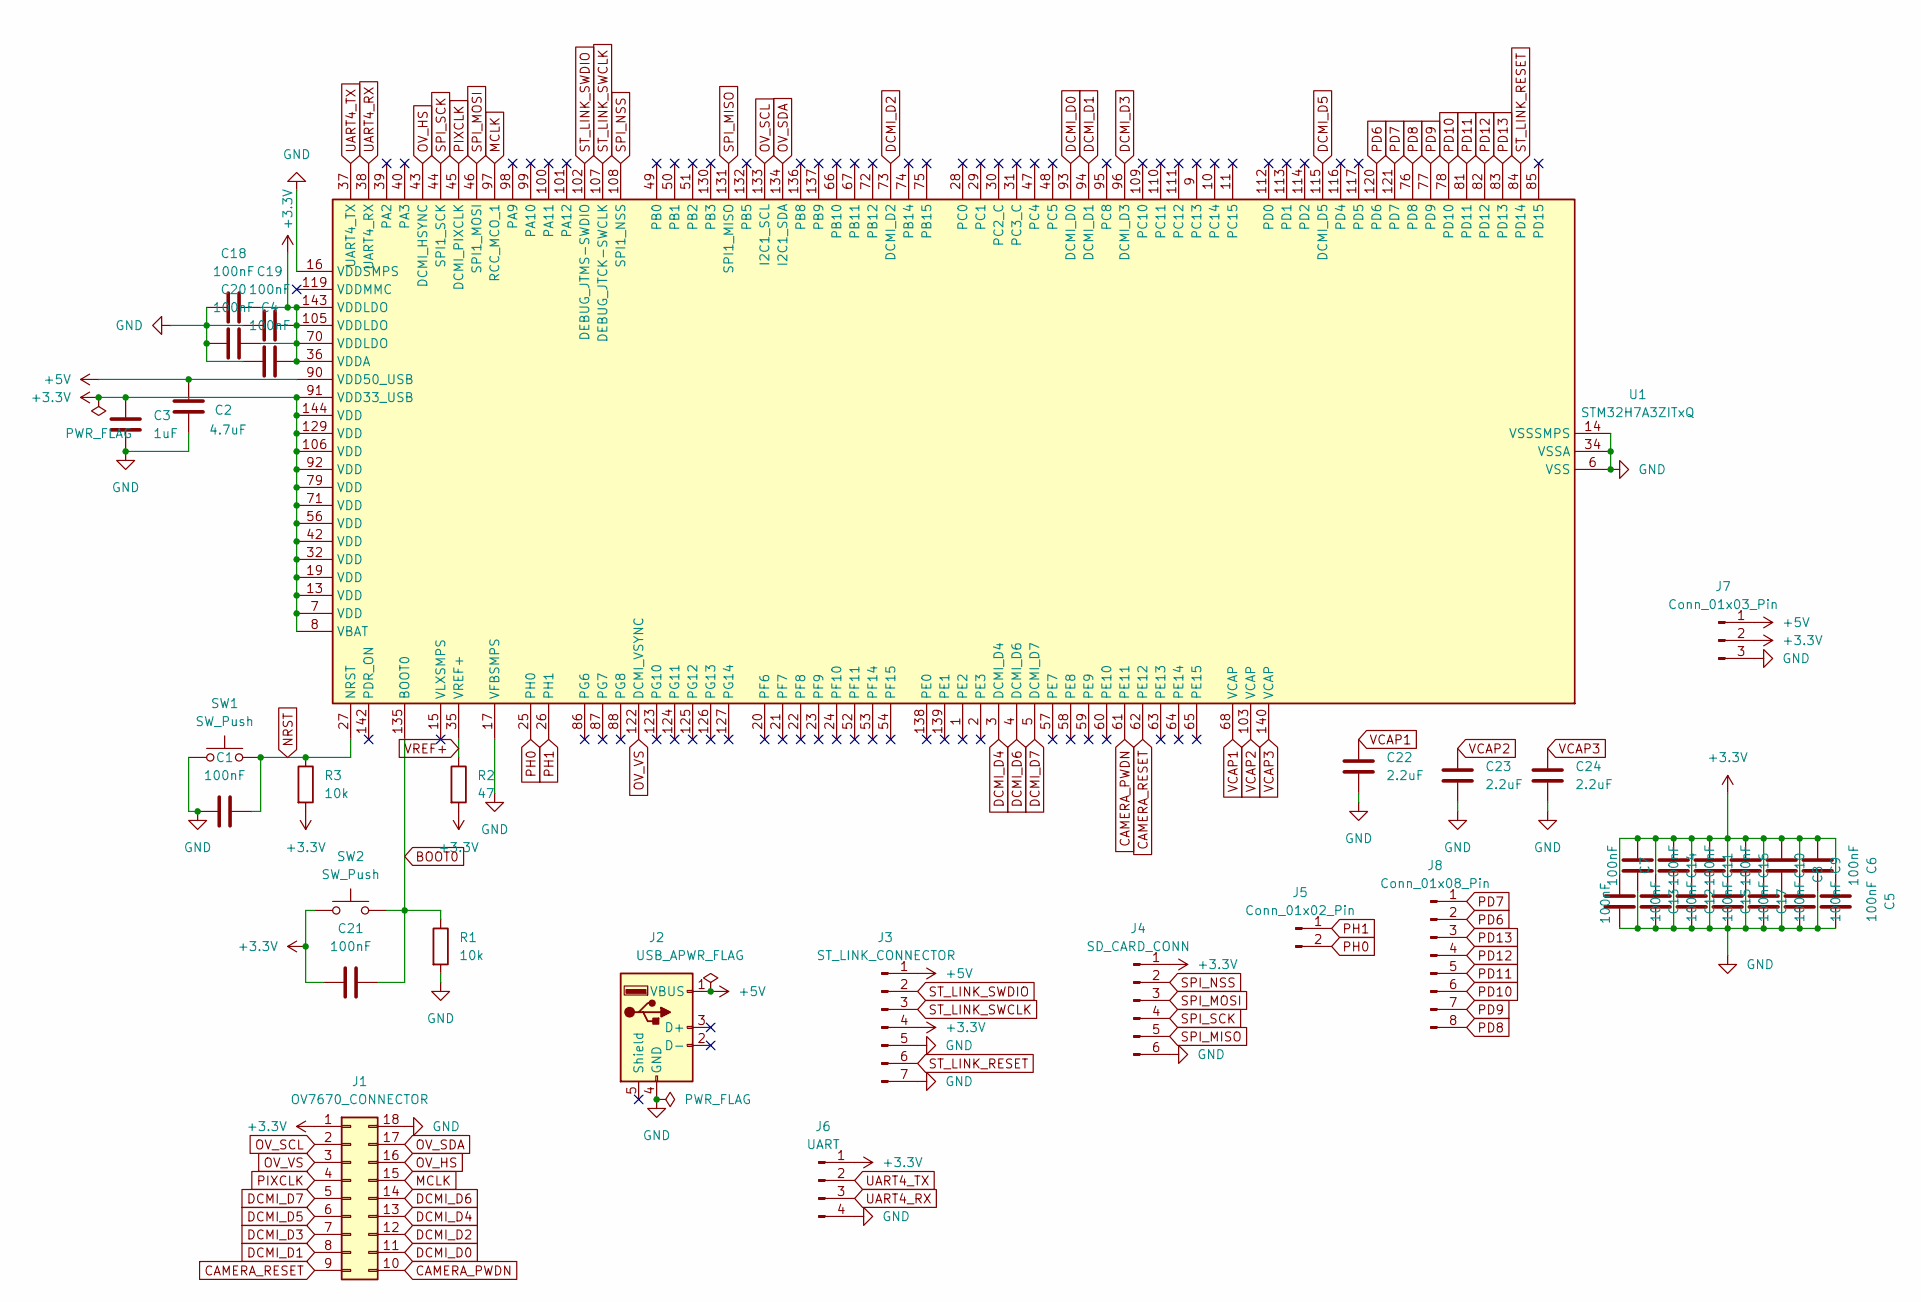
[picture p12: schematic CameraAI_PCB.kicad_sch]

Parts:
C1, C4, C5, C6, C7, C8, C9, C10, C11, C12, C13, C14, C15, C16, C17, C18, C19, C20, C21: 100nF; C_0805_2012Metric_Pad1.18x1.45mm_HandSolder
C2: 4.7uF; C_0805_2012Metric_Pad1.18x1.45mm_HandSolder
C3: 1uF; C_0805_2012Metric_Pad1.18x1.45mm_HandSolder
C22, C23, C24: 2.2uF; C_0805_2012Metric_Pad1.18x1.45mm_HandSolder
J1: OV7670_CONNECTOR; PinHeader_2x09_P2.54mm_Horizontal
J2: USB_A; USB3_A_Molex_48393-001
J3: ST_LINK_CONNECTOR; PinHeader_1x07_P2.54mm_Vertical
J4: SD_CARD_CONN; PinHeader_1x06_P2.54mm_Vertical
J5: Conn_01x02_Pin; PinHeader_1x02_P2.54mm_Vertical
J6: UART; PinHeader_1x04_P2.54mm_Vertical
J7: Conn_01x03_Pin; PinHeader_1x03_P2.54mm_Vertical
J8: Conn_01x08_Pin; PinHeader_1x08_P2.54mm_Vertical
R1, R3: 10k; R_0805_2012Metric_Pad1.20x1.40mm_HandSolder
R2: 47; R_0805_2012Metric_Pad1.20x1.40mm_HandSolder
SW1, SW2: SW_Push; Nidec_Copal_SH-7010A
U1: STM32H7A3ZITxQ; LQFP-144_20x20mm_P0.5mm

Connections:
+3.3V: C3.1, C4.1, C5.2, C6.2, C7.2, C8.2, C9.2, C10.2, C11.2, C12.2, C13.2, C14.2, C15.2, C16.2, C17.2, C18.1, C19.1, C20.1, C21.1, J1.1, J3.4, J4.1, J6.1, J7.2, R2.2, R3.2, SW2.1, U1.7 (VDD), U1.8 (VBAT), U1.13 (VDD), U1.19 (VDD), U1.32 (VDD), U1.36 (VDDA), U1.42 (VDD), U1.56 (VDD), U1.70 (VDDLDO), U1.71 (VDD), U1.79 (VDD), U1.91 (VDD33_USB), U1.92 (VDD), U1.105 (VDDLDO), U1.106 (VDD), U1.129 (VDD), U1.143 (VDDLDO), U1.144 (VDD)
+5V: C2.2, J2.1 (VBUS), J3.1, J7.1, U1.90 (VDD50_USB)
BOOT0: C21.2, R1.1, SW2.2, U1.135 (BOOT0)
CAMERA_PWDN: J1.10, U1.61 (PE11)
CAMERA_RESET: J1.9, U1.62 (PE12)
DCMI_D0: J1.11, U1.93 (DCMI_D0)
DCMI_D1: J1.8, U1.94 (DCMI_D1)
DCMI_D2: J1.12, U1.73 (DCMI_D2)
DCMI_D3: J1.7, U1.96 (DCMI_D3)
DCMI_D4: J1.13, U1.3 (DCMI_D4)
DCMI_D5: J1.6, U1.115 (DCMI_D5)
DCMI_D6: J1.14, U1.4 (DCMI_D6)
DCMI_D7: J1.5, U1.5 (DCMI_D7)
GND: C1.1, C2.1, C3.2, C4.2, C5.1, C6.1, C7.1, C8.1, C9.1, C10.1, C11.1, C12.1, C13.1, C14.1, C15.1, C16.1, C17.1, C18.2, C19.2, C20.2, C22.1, C23.1, C24.1, J1.18, J2.4 (GND), J3.5, J3.7, J4.6, J6.4, J7.3, R1.2, SW1.1, U1.6 (VSS), U1.12 (VSS), U1.14 (VSSSMPS), U1.16 (VDDSMPS), U1.17 (VFBSMPS), U1.18 (VSS), U1.33 (VSS), U1.34 (VSSA), U1.41 (VSS), U1.55 (VSS), U1.69 (VSS), U1.80 (VSS), U1.89 (VSS), U1.104 (VSS), U1.118 (VSS), U1.128 (VSS), U1.141 (VSS)
MCLK: J1.15, U1.97 (RCC_MCO_1)
NRST: C1.2, R3.1, SW1.2, U1.27 (NRST)
OV_HS: J1.16, U1.43 (DCMI_HSYNC)
OV_SCL: J1.2, U1.133 (I2C1_SCL)
OV_SDA: J1.17, U1.134 (I2C1_SDA)
OV_VS: J1.3, U1.122 (DCMI_VSYNC)
PD6: J8.2, U1.120 (PD6)
PD7: J8.1, U1.121 (PD7)
PD8: J8.8, U1.76 (PD8)
PD9: J8.7, U1.77 (PD9)
PD10: J8.6, U1.78 (PD10)
PD11: J8.5, U1.81 (PD11)
PD12: J8.4, U1.82 (PD12)
PD13: J8.3, U1.83 (PD13)
PH0: J5.2, U1.25 (PH0)
PH1: J5.1, U1.26 (PH1)
PIXCLK: J1.4, U1.45 (DCMI_PIXCLK)
SPI_MISO: J4.5, U1.131 (SPI1_MISO)
SPI_MOSI: J4.3, U1.46 (SPI1_MOSI)
SPI_NSS: J4.2, U1.108 (SPI1_NSS)
SPI_SCK: J4.4, U1.44 (SPI1_SCK)
ST_LINK_RESET: J3.6, U1.84 (PD14)
ST_LINK_SWCLK: J3.3, U1.107 (DEBUG_JTCK-SWCLK)
ST_LINK_SWDIO: J3.2, U1.102 (DEBUG_JTMS-SWDIO)
UART4_RX: J6.3, U1.38 (UART4_RX)
UART4_TX: J6.2, U1.37 (UART4_TX)
VCAP1: C22.2, U1.68 (VCAP)
VCAP2: C23.2, U1.103 (VCAP)
VCAP3: C24.2, U1.140 (VCAP)
VREF+: R2.1, U1.35 (VREF+)

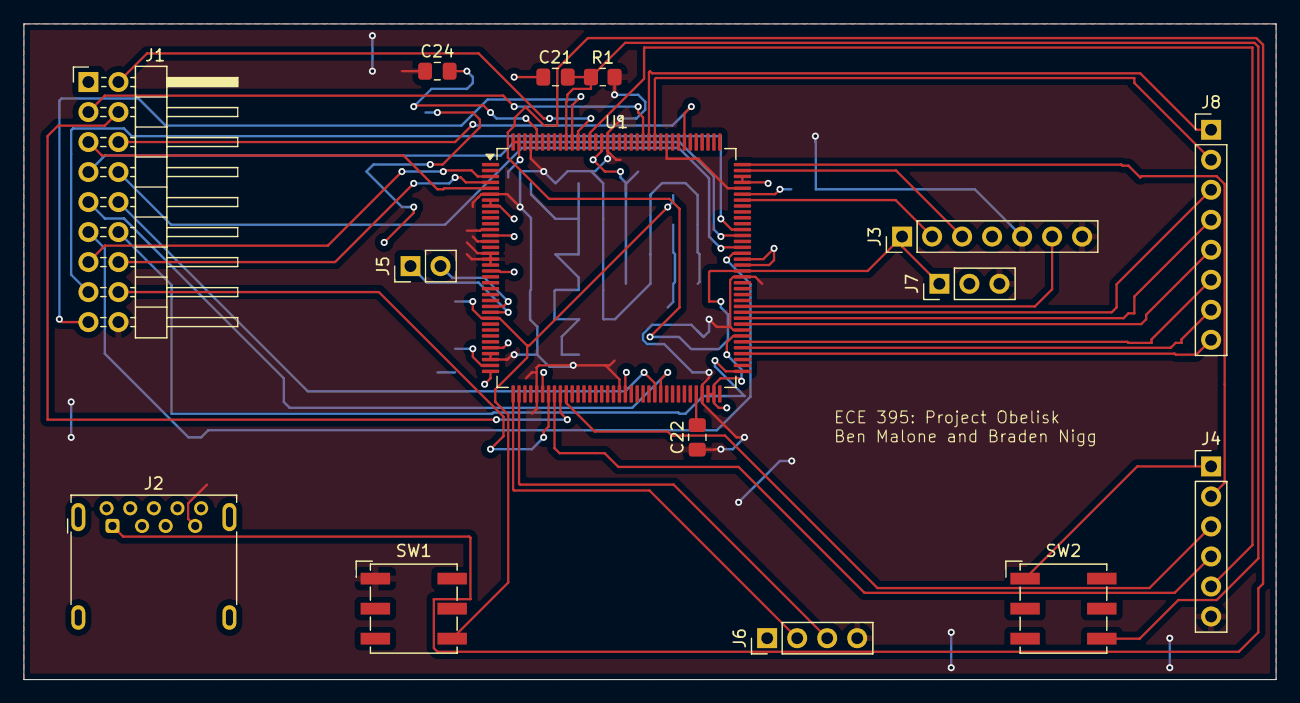
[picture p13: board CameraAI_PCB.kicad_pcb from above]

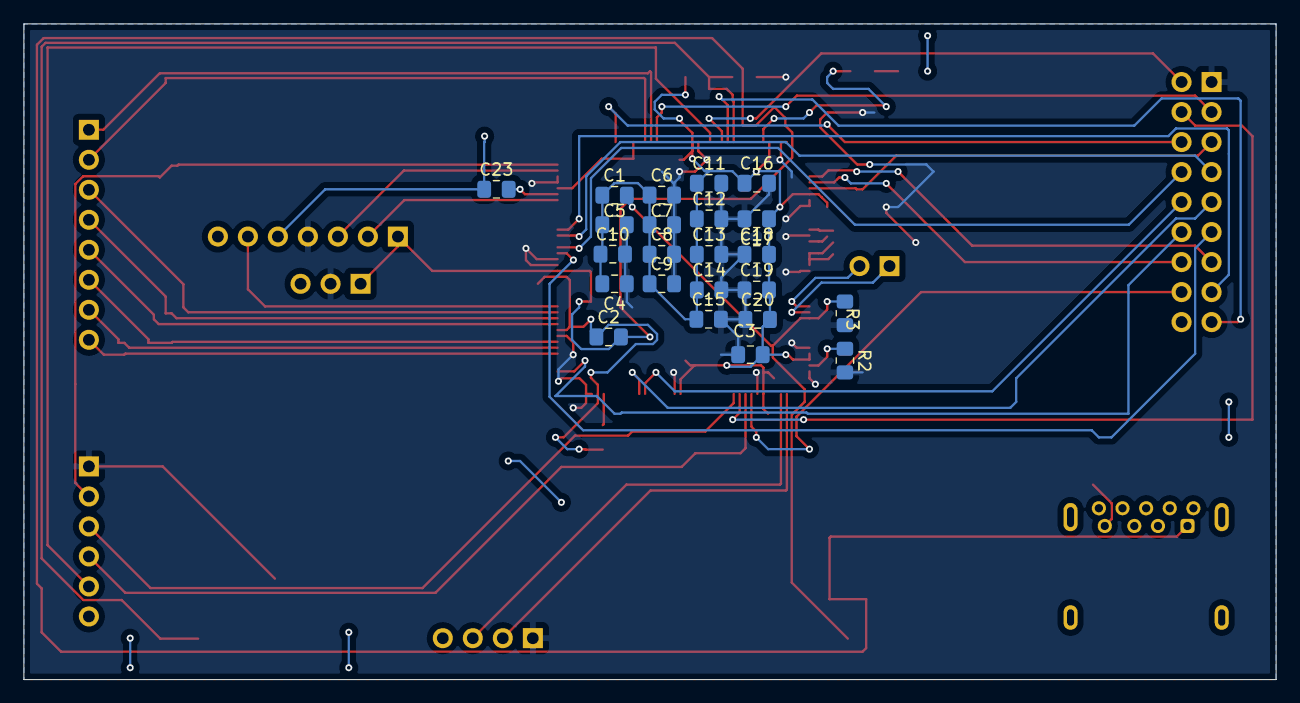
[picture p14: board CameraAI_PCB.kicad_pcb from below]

Board: 2 copper layers, 106.0 x 55.5 mm, 38 parts (23 on the bottom side), 44 nets.

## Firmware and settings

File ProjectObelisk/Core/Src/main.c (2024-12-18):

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
/* Includes ------------------------------------------------------------------*/
#include "main.h"

/* USER CODE BEGIN Includes */
#include "OV7670.h"
#include <stdint.h>

/* USER CODE END Includes */

/* USER CODE BEGIN PD */
#define TEST 1
/* USER CODE END PD */


DCMI_HandleTypeDef hdcmi;
DMA_HandleTypeDef hdma_dcmi;

I2C_HandleTypeDef hi2c1;

SPI_HandleTypeDef hspi1;

TIM_HandleTypeDef htim4;

UART_HandleTypeDef huart4;

void SystemClock_Config(void);
static void MPU_Config(void);
static void MX_GPIO_Init(void);
static void MX_DMA_Init(void);
static void MX_DCMI_Init(void);
static void MX_I2C1_Init(void);
static void MX_SPI1_Init(void);
static void MX_UART4_Init(void);
static void MX_TIM4_Init(void);
/* USER CODE BEGIN 0 */

Camera_settings OV7670_settings={
	QVGA, 		//Resolution
	RGB565, 	//Format
};

// Local Constants ----------------------------------
#define QVGA 320 * 240

// Global Variables ---------------------------------
uint16_t image_data[QVGA];
uint8_t formated_img[QVGA*3];	// Three bytes per pixel
uint16_t width, height;
uint8_t format;

static void format_image(uint8_t * p_img);
static void setServoAngle(uint32_t angle);

#if TEST
static void send_image(uint8_t *formatted_image, uint32_t image_size);
#endif

/* USER CODE END 0 */

/**
  * @brief  The application entry point.
  * @retval int
  */
int main(void)
{

  /* MPU Configuration--------------------------------------------------------*/
  MPU_Config();

  /* MCU Configuration--------------------------------------------------------*/

  /* Reset of all peripherals, Initializes the Flash interface and the Systick. */
  HAL_Init();

  /* Configure the system clock */
  SystemClock_Config();

  /* Initialize all configured peripherals */
  MX_GPIO_Init();
  MX_DMA_Init();
  MX_DCMI_Init();
  MX_I2C1_Init();
  MX_SPI1_Init();
  MX_UART4_Init();
  MX_TIM4_Init();
  /* USER CODE BEGIN 2 */
  OV7670_Power(DISABLE);
  OV7670_Init(&hdcmi, &hdma_dcmi, &hi2c1);

  OV7670_Power(ENABLE);
  OV7670_SetFrameControl(168,24,12,492);
  HAL_Delay(10);

  OV7670_Start(CONTINUOUS, image_data);			// Continous Mode fixed DMA transfer issue, can be used like snapshot
  OV7670_getImageInfo(&width,&height,&format);
  HAL_Delay(100);
  HAL_TIM_PWM_Start(&htim4, TIM_CHANNEL_1);

  // #TODO: Set GPIOS for LED start state
  // #TODO: Convert ProjectObelisk_RaspPI_Arduino/CameraAI.py into C code

  /* USER CODE END 2 */

  /* Infinite loop */
  /* USER CODE BEGIN WHILE */
  while (1)
  {
	  // #TODO: Implement Control loop - Reference ProjectObelisk_RaspPI_Arduino/control_loop.py for intended behavior]
	  setServoAngle(0);
	  while(!frame_ready)
	  {}
	  format_image(formated_img);
#if TEST
	  send_image(formated_img, QVGA*3);
#endif
	  // #TODO: Implement decider result - Reference ProjectObelisk_RaspPI_Arduino/control_loop.py for intended behavior
	  setServoAngle(180);
    /* USER CODE END WHILE */

    /* USER CODE BEGIN 3 */
  }
  /* USER CODE END 3 */
}

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
/* USER CODE BEGIN 4 */

// Function to format the image data for RGB565 format and populate the output buffer
void format_image(uint8_t * p_img) {
    uint32_t word = 0;         // Temporary variable to store a 32-bit word from image data
    uint32_t length = 0;       // Counter to track the position in the output buffer

    // Loop through each pixel pair (two pixels per 32-bit word)
    for (uint16_t i = 0; i < width / 2; i++) {
        for (uint16_t j = 0; j < height; j++) {
            word = image_data[j + i * (width / 2)]; // Access the image data for the current pixel pair

            if (format == RGB565) { // Check if the format is RGB565
                // Extract the red component (5 bits from the upper 16 bits)
                uint8_t R = (uint8_t)(((word >> 16) & 0xF800) >> 11);
                // Extract the green component (6 bits from the upper 16 bits)
                uint8_t G = (uint8_t)(((word >> 16) & 0x07E0) >> 5);
                // Extract the blue component (5 bits from the upper 16 bits)
                uint8_t B = (uint8_t)((word >> 16) & 0x001F);

                // Store the RGB components in the output buffer sequentially
                p_img[length++] = R;
                p_img[length++] = G;
                p_img[length++] = B;
            }
        }
    }
}

// Function to set the servo angle based on a specified value (0-180 degrees)
void setServoAngle(uint32_t angle) {
    if (angle > 180) angle = 180; // Limit the angle to the maximum value of 180 degrees

    int32_t minPulseWidth = 1000; // Minimum pulse width (1ms) for 0 degrees
    int32_t maxPulseWidth = 2000; // Maximum pulse width (2ms) for 180 degrees

    // Calculate the pulse width corresponding to the specified angle
    uint32_t pulse = (uint32_t)((angle * (maxPulseWidth - minPulseWidth)) / 180) + minPulseWidth;

    // Set the pulse width for the timer's PWM channel to control the servo
    TIM2->CCR2 = pulse;
}

#if TEST
#define CHUNK_SIZE 240  // Maximum size of each data chunk to be sent (must be a multiple of 3 for RGB format)

// Function to send a formatted image over UART in chunks. Note uint16_t is max size, and our image is bigger
void send_image(uint8_t *formatted_image, uint32_t image_size) {
    uint32_t bytes_sent = 0;    // Counter to track the number of bytes sent

    // Continue until all bytes in the image are sent
    while (bytes_sent < image_size) {
        uint32_t bytes_to_send = image_size - bytes_sent;

        // Ensure the size of the current chunk does not exceed the defined maximum chunk size
        if (bytes_to_send > CHUNK_SIZE) {
            bytes_to_send = CHUNK_SIZE;
        }

        // Transmit the current chunk over UART
        HAL_StatusTypeDef status = HAL_UART_Transmit(&huart4, &formatted_image[bytes_sent], bytes_to_send, HAL_MAX_DELAY);

        // Handle any transmission errors
        if (status != HAL_OK) {
            // Log or handle transmission error
            return;
        }

        // Update the byte counter after successfully transmitting the chunk
        bytes_sent += bytes_to_send;
    }
}
#endif


/* USER CODE END 4 */

 /* MPU Configuration */

void MPU_Config(void)
{
  MPU_Region_InitTypeDef MPU_InitStruct = {0};

  /* Disables the MPU */
  HAL_MPU_Disable();

  /** Initializes and configures the Region and the memory to be protected
  */
  MPU_InitStruct.Enable = MPU_REGION_ENABLE;
  MPU_InitStruct.Number = MPU_REGION_NUMBER0;
  MPU_InitStruct.BaseAddress = 0x0;
  MPU_InitStruct.Size = MPU_REGION_SIZE_4GB;
  MPU_InitStruct.SubRegionDisable = 0x87;
  MPU_InitStruct.TypeExtField = MPU_TEX_LEVEL0;
  MPU_InitStruct.AccessPermission = MPU_REGION_NO_ACCESS;
  MPU_InitStruct.DisableExec = MPU_INSTRUCTION_ACCESS_DISABLE;
  MPU_InitStruct.IsShareable = MPU_ACCESS_SHAREABLE;
  MPU_InitStruct.IsCacheable = MPU_ACCESS_NOT_CACHEABLE;
  MPU_InitStruct.IsBufferable = MPU_ACCESS_NOT_BUFFERABLE;

  HAL_MPU_ConfigRegion(&MPU_InitStruct);
  /* Enables the MPU */
  HAL_MPU_Enable(MPU_PRIVILEGED_DEFAULT);

}

/**
  * @brief  This function is executed in case of error occurrence.
  * @retval None
  */
void Error_Handler(void)
{
  /* USER CODE BEGIN Error_Handler_Debug */
  /* User can add his own implementation to report the HAL error return state */
  __disable_irq();
  while (1)
  {
  }
  /* USER CODE END Error_Handler_Debug */
}

#ifdef  USE_FULL_ASSERT
/**
  * @brief  Reports the name of the source file and the source line number
  *         where the assert_param error has occurred.
  * @param  file: pointer to the source file name
  * @param  line: assert_param error line source number
  * @retval None
  */
void assert_failed(uint8_t *file, uint32_t line)
{
  /* USER CODE BEGIN 6 */
  /* User can add his own implementation to report the file name and line number,
     ex: printf("Wrong parameters value: file %s on line %d\r\n", file, line) */
  /* USER CODE END 6 */
}
#endif /* USE_FULL_ASSERT */

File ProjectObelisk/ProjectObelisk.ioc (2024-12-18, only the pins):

Mcu.UserName=STM32H7A3ZITxQ
PA0.Signal=UART4_TX
PA1.Signal=UART4_RX
PA13.Signal=DEBUG_JTMS-SWDIO
PA14.Signal=DEBUG_JTCK-SWCLK
PA15.Signal=SPI1_NSS
PA4.Signal=DCMI_HSYNC
PA5.Signal=SPI1_SCK
PA6.Signal=DCMI_PIXCLK
PA7.Signal=SPI1_MOSI
PA8.Signal=RCC_MCO_1
PB13.Signal=DCMI_D2
PB4.Signal=SPI1_MISO
PB6.Signal=I2C1_SCL
PB7.Signal=I2C1_SDA
PC6.Signal=DCMI_D0
PC7.Signal=DCMI_D1
PC9.Signal=DCMI_D3
PD10.GPIO_Label=TRAIN_IMG1_BUTTON
PD10.Signal=GPIO_Input
PD11.GPIO_Label=TRAIN_IMG2_BUTTON
PD11.Signal=GPIO_Input
PD12.GPIO_Label=SERVO_PWM
PD12.Signal=S_TIM4_CH1
PD3.Signal=DCMI_D5
PD6.GPIO_Label=GREEN_LED
PD6.Signal=GPIO_Output
PD7.GPIO_Label=RED_LED
PD7.Signal=GPIO_Output
PD8.GPIO_Label=BLUE_LED
PD8.Signal=GPIO_Output
PD9.GPIO_Label=DECIDER_BUTTON
PD9.Signal=GPIO_Input
PE11.GPIO_Label=CAMERA_PWDN
PE11.Signal=GPIO_Output
PE12.GPIO_Label=CAMERA_RESET
PE12.Signal=GPIO_Output
PE4.Signal=DCMI_D4
PE5.Signal=DCMI_D6
PE6.Signal=DCMI_D7
PG9.Signal=DCMI_VSYNC

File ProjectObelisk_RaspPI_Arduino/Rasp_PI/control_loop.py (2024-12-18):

from PIL import Image
import scipy.signal as sg
import sys
import numpy as np
import serial
import os
from cameraAI import *  # Import custom AI-related functions
from gpio import *  # Import custom GPIO control functions
from uart import *  # Import custom UART-related functions

def main():
    """
    Main function to control a servo and LED system based on button inputs and AI decisions.
    It initializes devices, enters an infinite loop to handle button events, and controls
    LEDs and servo movements according to the logic.
    """
    GPIO.cleanup()  # Ensure clean GPIO state before starting
    
    # Initialize devices
    pwm = init_servo()  # Initialize servo motor
    control_servo(pwm, 0)  # Ensure servo starts in the locked position
    init_button()  # Set up buttons
    init_LED()  # Set up LEDs
    
    # Flash all LEDs for initialization indication
    set_LED(GREEN_LED_PIN, 1)
    set_LED(RED_LED_PIN, 1)
    set_LED(BLUE_LED_PIN, 1)
    time.sleep(2)
    set_LED(GREEN_LED_PIN, 0)
    set_LED(RED_LED_PIN, 0)
    set_LED(BLUE_LED_PIN, 0)
    
    # Main loop to process button inputs and control devices
    while True:
        try:
            # Wait for a button press and get the button index
            button_key = wait_for_button()
            print("Button pressed:", button_key)
            
            if button_key == 0:  # Run AI model on captured image
                set_LED(GREEN_LED_PIN, 0)
                set_LED(RED_LED_PIN, 0)
                set_LED(BLUE_LED_PIN, 1)  # Indicate capture in progress
                capture = request_capture()  # Capture an image
                
                if decide(capture):  # Use AI model to decide on the capture
                    # Capture accepted: Unlock and indicate success
                    set_LED(GREEN_LED_PIN, 1)
                    set_LED(RED_LED_PIN, 0)
                    control_servo(pwm, 180)  # Unlock position
                    time.sleep(5)
                    control_servo(pwm, 0)  # Lock position
                    set_LED(GREEN_LED_PIN, 0)
                    set_LED(RED_LED_PIN, 1)
                else:
                    # Capture rejected: Indicate failure with blinking red LED
                    set_LED(RED_LED_PIN, 1)
                    set_LED(GREEN_LED_PIN, 0)
                    for _ in range(3):
                        time.sleep(0.5)
                        set_LED(RED_LED_PIN, 0)
                        time.sleep(0.5)
                        set_LED(RED_LED_PIN, 1)
                    control_servo(pwm, 0)  # Ensure servo remains locked
                
                set_LED(BLUE_LED_PIN, 0)  # Turn off blue LED
            
            elif button_key == 1:  # Retrain training image 1
                set_LED(GREEN_LED_PIN, 0)
                set_LED(RED_LED_PIN, 0)
                set_LED(BLUE_LED_PIN, 1)  # Indicate capture in progress
                capture = request_capture()  # Capture an image
                capture.save("/home/bnigg17/Documents/ECE395/Obelisk_RaspPI/training_1.png")  # Save image
                set_LED(GREEN_LED_PIN, 0)
                set_LED(RED_LED_PIN, 1)  # Indicate success
                set_LED(BLUE_LED_PIN, 0)
            
            elif button_key == 2:  # Retrain training image 2
                set_LED(GREEN_LED_PIN, 0)
                set_LED(RED_LED_PIN, 0)
                set_LED(BLUE_LED_PIN, 1)  # Indicate capture in progress
                capture = request_capture()  # Capture an image
                capture.save("/home/bnigg17/Documents/ECE395/Obelisk_RaspPI/training_2.png")  # Save image
                set_LED(GREEN_LED_PIN, 0)
                set_LED(RED_LED_PIN, 1)  # Indicate success
                set_LED(BLUE_LED_PIN, 0)
        
        except KeyboardInterrupt:
            # Handle keyboard interrupt (Ctrl+C) to exit the program
            print("Keyboard interrupt detected. Exiting...")
            pwm.stop()  # Stop the PWM signal
            GPIO.cleanup()  # Reset GPIO settings to default state
            break


if __name__ == "__main__":
    """
    Entry point for the script. Calls the main function to start the program.
    """
    main()

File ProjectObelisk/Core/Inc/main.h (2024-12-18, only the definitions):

#define CAMERA_PWDN_Pin GPIO_PIN_11
#define CAMERA_PWDN_GPIO_Port GPIOE
#define CAMERA_RESET_Pin GPIO_PIN_12
#define CAMERA_RESET_GPIO_Port GPIOE
#define BLUE_LED_Pin GPIO_PIN_8
#define BLUE_LED_GPIO_Port GPIOD
#define DECIDER_BUTTON_Pin GPIO_PIN_9
#define DECIDER_BUTTON_GPIO_Port GPIOD
#define TRAIN_IMG1_BUTTON_Pin GPIO_PIN_10
#define TRAIN_IMG1_BUTTON_GPIO_Port GPIOD
#define TRAIN_IMG2_BUTTON_Pin GPIO_PIN_11
#define TRAIN_IMG2_BUTTON_GPIO_Port GPIOD
#define SERVO_PWM_Pin GPIO_PIN_12
#define SERVO_PWM_GPIO_Port GPIOD
#define GREEN_LED_Pin GPIO_PIN_6
#define GREEN_LED_GPIO_Port GPIOD
#define RED_LED_Pin GPIO_PIN_7
#define RED_LED_GPIO_Port GPIOD

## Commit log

2024-09-23 Initialize repo, gitignore, and first subproject upload with Servo
2024-09-30 added a printing output function, done with creating cam ports
2024-10-04 began writing communication functions for camera
2024-10-05 Isolated camera code, switched write to i2c protocol
2024-10-28 Switched to DCMI pclk looks nice
2024-10-29 CameraAI has working vsync and href
2024-10-31 Camera finally showing some life
2024-11-04 Print image is much cleaner
2024-11-12 Got partial image, need to scale and color calibrate
2024-11-27 DMA Broke
2024-12-08 Serial Driver
2024-12-10 demo stage1
    [pyvenv.cfg]
2024-12-18 Upload PCB
    [CameraAI_PCB-B_Cu.gbr, CameraAI_PCB-B_Mask.gbr, CameraAI_PCB-B_Paste.gbr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]
2024-12-18 Ready for Submission
    [CameraAI_PCB-B_Cu.gbr, CameraAI_PCB-B_Mask.gbr, CameraAI_PCB-B_Paste.gbr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]

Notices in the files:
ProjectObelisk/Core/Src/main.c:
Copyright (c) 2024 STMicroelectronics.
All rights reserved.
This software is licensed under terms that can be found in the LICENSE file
